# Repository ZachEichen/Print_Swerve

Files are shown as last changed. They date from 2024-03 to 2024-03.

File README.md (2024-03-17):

# Print Swerve: A fully customizable, Fully 3D printable Swerve drive for FTC 

This is a fully 3d printable swerve drive developed and used by FTC team [Robocracy](http://www.ftcrobocracy.org) in the 2018 FTC searon. It was primarily developed by [Nicolas Eichenberger](https://sites.google.com/view/neichenberger/) and [Zachary Eichenberger](https://github.com/ZachEichen).

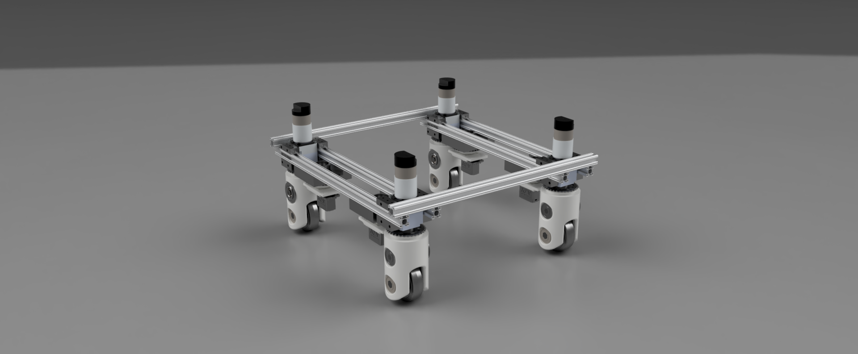
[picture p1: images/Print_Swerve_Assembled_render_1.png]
A render of the printable swerve assembled


As an FTC team we always strive to push the competition to the next level. We spent over a year developing our very own swerve drive to be a viable FTC drive base. 
After so much time and effort spent in development, we have developed the very first fully 3D printable swerve drive viable for FTC. Finally we have gotten this competition tested design to a stage of completion. 
Therefore, we are releasing this design for the benefit of the FTC community, and anyone else interested in an interesting omnidirectional robot drivetrain. 

## Using this repository: 

Both STL files for printing, and full CAD assemblies are avaliable for convenience. I have exported these in a variety of common CAD file formats in `CAD_source` (although they were made in fusion 360 so they might be a little wonky). 

Two STL files of the main module are avaliable. Our assembly guide assumes the use of 1/2" flanged thunderhex bearings from Vexpro. To use this part, print `STL_files/ModuleBody.stl`. Otherwise, you can use radial thunderHex bearings, and substitute `Tube_Body_Radial_Bearings.stl`.

You can also have a look at the associated thingiverse part, [found here](https://www.thingiverse.com/thing:2998874/files), and Nicky's [blog post](https://sites.google.com/view/neichenberger/projects/robotics-projects/swerve-drive-saga)  on the build process. 

## Glamour shots 

https://github.com/ZachEichen/Print_Swerve/assets/14967701/36f6d081-fa3b-49ac-bc39-774735051941

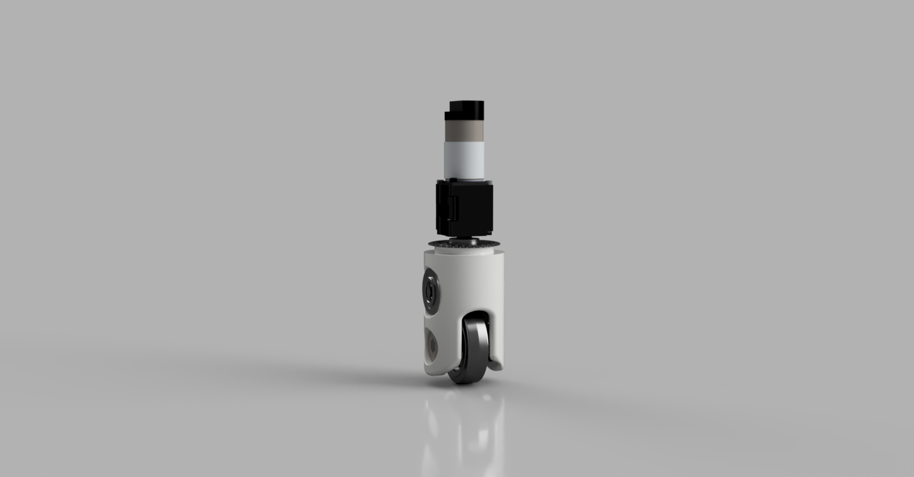
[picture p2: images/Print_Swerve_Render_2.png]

Glam shot

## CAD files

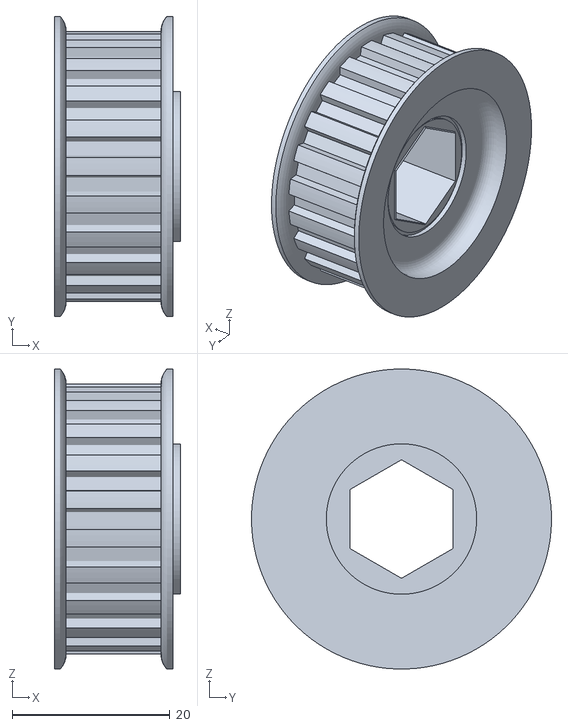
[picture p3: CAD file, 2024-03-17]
STL_files/ModuleBottomPulley.stl
16.0 x 38.0 x 38.0

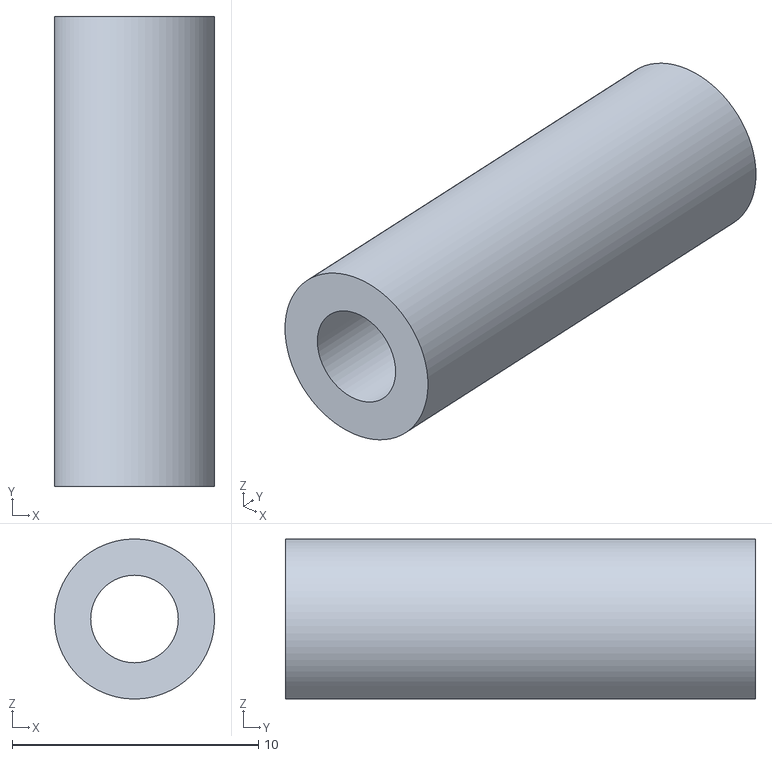
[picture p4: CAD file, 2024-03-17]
STL_files/Steering_Module_Standoffs.stl
6.50 x 19.1 x 6.49

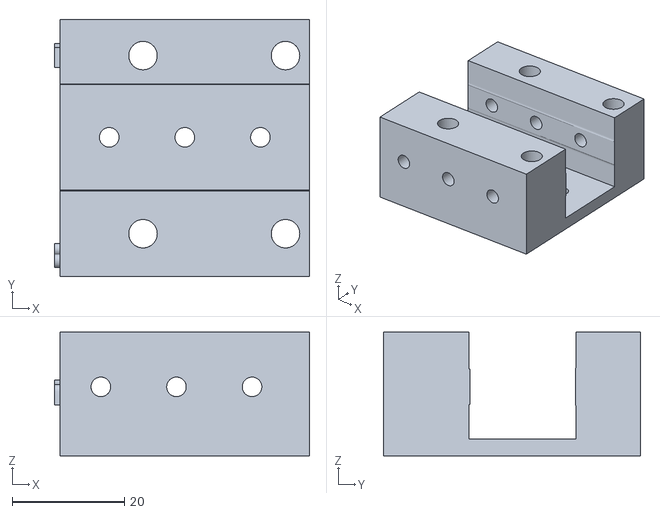
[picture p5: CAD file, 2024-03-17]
STL_files/RightMotorMount.stl
45.5 x 45.7 x 22.1

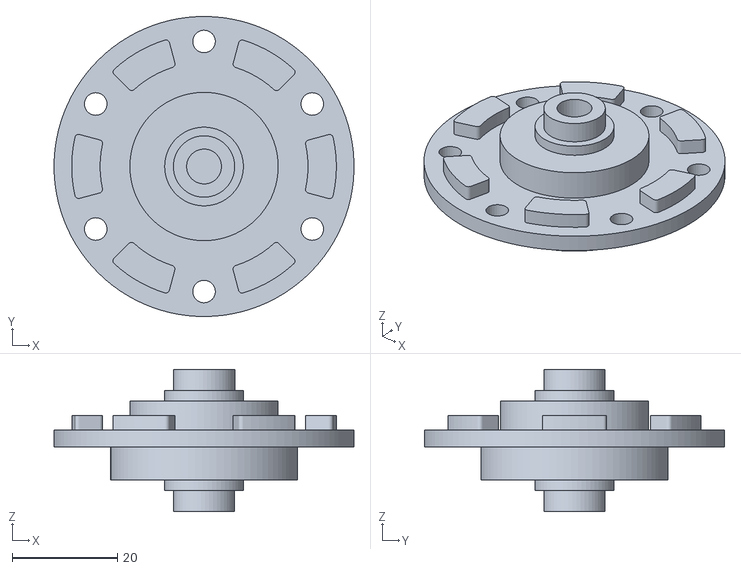
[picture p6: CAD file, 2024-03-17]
STL_files/Sprocket_Adapter_Plate.stl
57.1 x 57.1 x 27.1

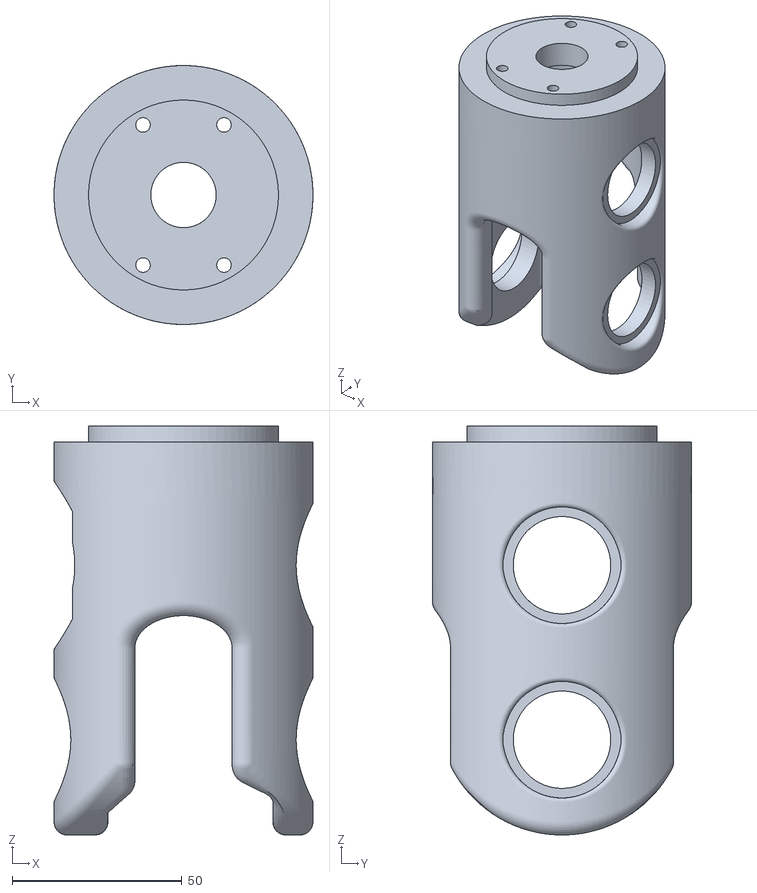
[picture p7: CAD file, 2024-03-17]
STL_files/ModuleBody.stl
76.2 x 76.2 x 120.3

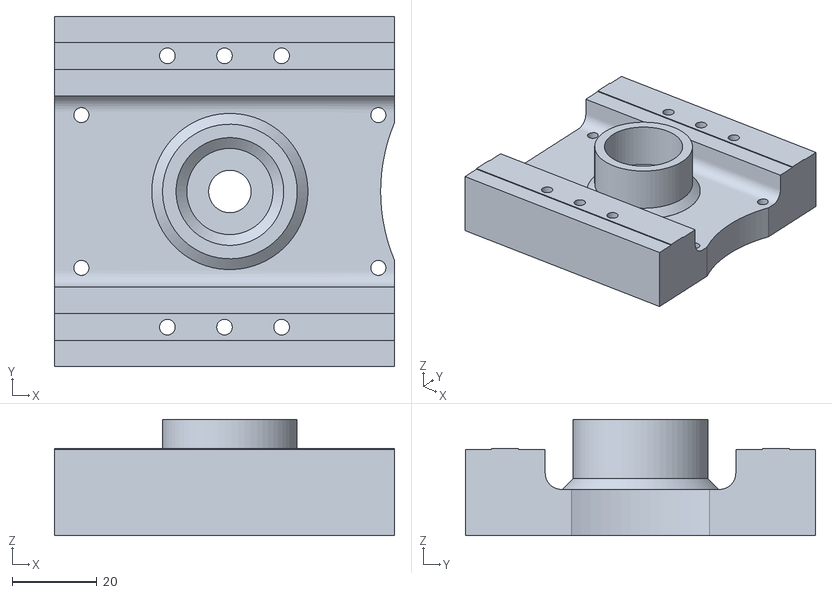
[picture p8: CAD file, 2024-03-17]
STL_files/Steering_Module_Top_Plate.stl
80.2 x 82.6 x 27.4

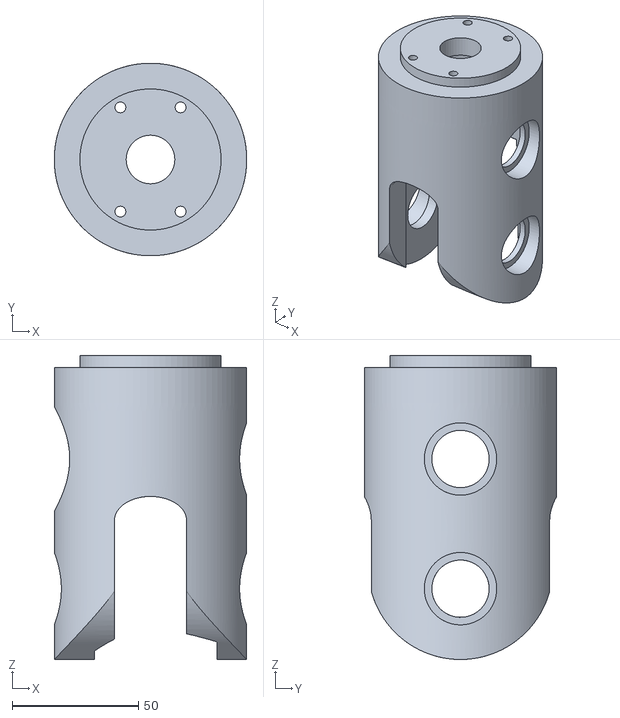
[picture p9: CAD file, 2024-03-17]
STL_files/Tube_Body_Radial_Bearings.stl
76.2 x 76.2 x 120.3

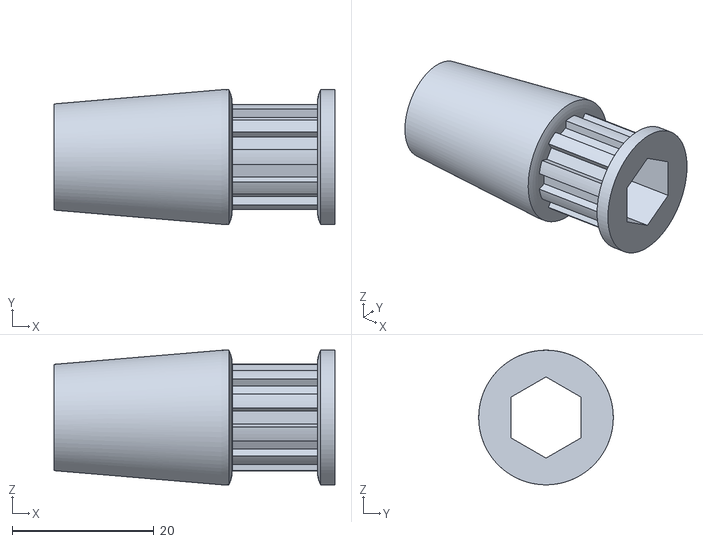
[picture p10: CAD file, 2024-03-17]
STL_files/ModuleTopPulley.stl
39.7 x 19.0 x 19.0

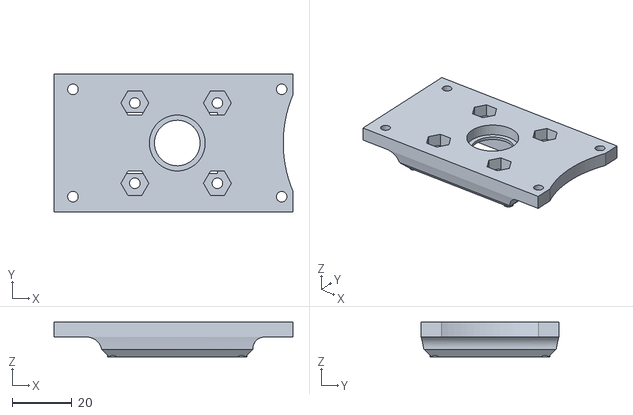
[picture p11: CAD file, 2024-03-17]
STL_files/Steering_Module_Bottom_Plate.stl
80.2 x 46.2 x 11.6

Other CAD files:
STL_files/leftMotorMount.stl

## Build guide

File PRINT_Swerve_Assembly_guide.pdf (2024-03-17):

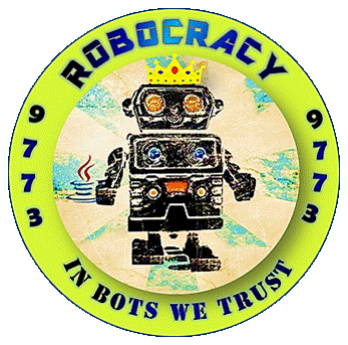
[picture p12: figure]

# PRINT Swerve Drive for FTC

Designed and built by Team FTC 9773, Robocracy 4H Westchester, NY
ftcrobocracy@gmail.com
March 2018

# 1.Introduction

We provide here the full instruction on how to build your very own PRINT Swerve. This innovative swerve drive is entirely build out of 3D printed part, no CNC machining required. It uses FRC-level gears and sprockets (VEX-pro) for unprecedented reliability. We use a novel “Tower” design where the drive motor is directly mounted on top of the drive to deliver the compact footprint needed for FTC robots. To our knowledge, this is the first 3D printable, nearly-indestructible integrated swerve drive, optimized for the tight spaces using FRC-level gears. We named it PRINT Swerve module, for PRintable INtegrated Tower Swerve.

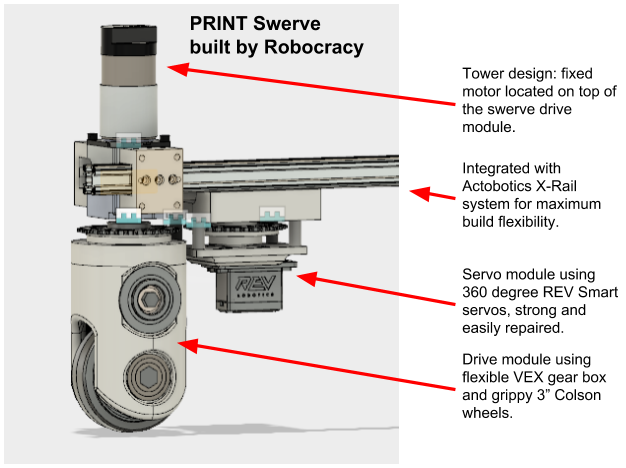
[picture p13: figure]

You will need between 2 to 4 Swerve Drive Modules, typically 4. A Swerve Drive Module consists of two assemblies: a Motor Module and a Steering Module. The two are connected by a chain and are mounted on a chassis made of Actobotics X-Rails. The Colson wheel has a 3” diameter, sufficient for climbing most obstacles. Once you have assembled the 122 parts, you will own your very own PRINT Swerve drive.

Section 2 list the parts that you need to build one Swerve Drive. For each part, we list a vendor and its part number. Section 3 lists the parts that you will need to 3D print, and Section 4 details the tools required to build it. Section 5 provides a step by step description and illustration of how to build the Swerve Motor Module. Section 6 details how to build the Swerve Steering Module. Section 7 let you assemble the two modules on the X-rails.

# 2. List of parts

## 2.1 Parts for the Swerve Motor Module

Part name | # | Part description | Part number
Motor (1) | 1 | AndyMark NeveRest Classic Motor | AndyMark part am-3104
Gear box (2) | 1 | VersaPlanetary Gearbox with ⅜ hex shaft with recommended 9:1 gear ratio. You may want to buy a spare VersaPlanetary 3/8" Hex Output Shaft as you will need to tap the end. | VEX PRO ● Base kit ⅜ Hex output, part 217-4974 ● 9:1 Gear kit part 217-3106 ● Ring gear part 217-2816 ● Additional shaft part 217-2894 (optional)

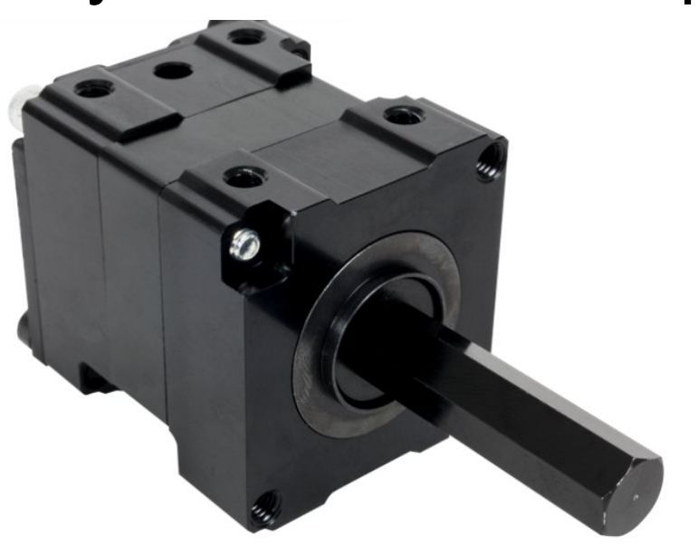
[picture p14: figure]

⅜” Flanged ball bearing (3) | 2 | Flanged ball bearing for ⅜ shaft, 0.375" Hex ID x 1.125" OD x 0.313" WD | VEX-pro part 217-2735

PRINT Swerve Drive for FTC, by Team FTC 9773, Robocracy 4H.
Web: ftcrobocray.org, email: ftcrobocracy@gmail.com. | Page 2 of 20.

Thunderhex flanged ball bearing (4) | 2 | Flanged ball bearing for 1/2" ThunderHex ½” ID x 1.125" OD x 0.313" WD | VEX-pro part 217-4006
Alternator ball bearing (5) | 1 | AB Open Alternator Ball Bearing 18.7mm x 37mm x9mm | VXB part 6904DW
Large flanged ball bearing (6) | 1 | Flanged ball bearing for 3/4" Shaft Diameter, 1-5/8" OD | McMaster part 6384K367
Bevel gear (7) | 2 | 15t Steel Bevel Gear, 12DP, 3/8" Hex Bore | VEX-pro part 217-3344
Wheel (8) | 1 | Colson Performa wheel, 3" x 0.875", 1/2" Hex Bore | VEX-pro part 217-4047
Web: ftcrobocray.org, email: ftcrobocracy@gmail.com. | Page 3 of 20.

Timing belt (9) | 1 | 185mm timing belt Dust-Free Timing Belt, T5 Series, Trade No. T5-185-1 | McMaster part 1679K441
½” Thunderhex shaft (10) | 2.6” | thunderhex shaft ½” | VEX-pro part 217-4002
⅜” Hex shaft (11) | 2.75” | Hex shaft ⅜” | VEX-pro part 217-3310
Sprocket (12) | 1 | 32t Aluminum Plate Sprocket for #25 Chain, 1-1/8" Bearing Bore | VEX-pro part 217-2690
Chain (13) | 12” | #25 Standard Roller Chain (10 feet) | VEX-pro part 217-2775
Web: ftcrobocray.org, email: ftcrobocracy@gmail.com. | Page 4 of 20.

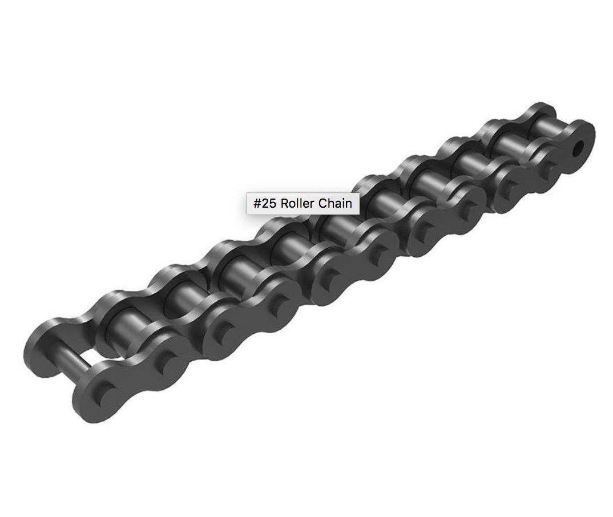
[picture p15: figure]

¼” Screw (14) | 2 | 18-8 Stainless Steel Button Head Hex Drive Screw, 1/4"-20 Thread Size, 3/4" Long | McMaster part 92949A540
#8 Screw (15) | 3 | 18-8 Stainless Steel Button Head Hex Drive Screw, 8-32 Thread Size, 1/2" Long | McMaster part 92949A194

Long #6 Screw and nylon nut (part 16) | 4 | 18-8 Stainless Steel Button Head Hex Drive Screw, 6-32 Thread Size, 1" Long 316 Stainless Steel Nylon-Insert Locknut, Super-Corrosion-Resistant, 6-32 Thread Size | McMaster parts 92949A153 and 90715A007
Large #8 washer (17) | 1 | 316 Stainless Steel Washer, Oversized, Number 8 Screw Size, 0.188" ID, 1" OD | McMaster part 91525A268
Small #8 | 1 | 316 Stainless Steel Washer, Oversized, | McMaster part
Web: ftcrobocray.org, email: ftcrobocracy@gmail.com. | Page 5 of 20.

washer (18) | | Number 8 Screw Size, 0.172" ID, 0.5" OD | 91525A318

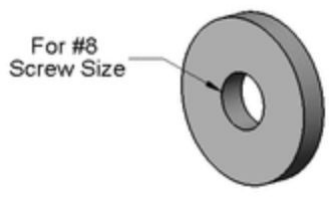
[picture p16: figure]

Very small #8 washer (19) | 1 | 18-8 Stainless Steel Washer for Number 8 Screw Size, 0.172" ID, 0.375" OD | McMaster part 92141A009
¼” washer (20) | 2 | 316 Stainless Steel Washer for 1/4" Screw Size, 0.281" ID, 0.625" OD | McMaster part 90107A029

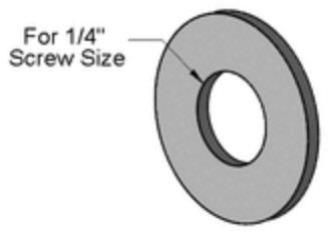
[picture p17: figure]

Hex spacer (21) | 1 | 1/2" Acetal Spacer - 1/2" Hex (10-pack) | VEX-pro part 217-3261
Hex spacer (22) | 1 | 1/8” Acetal Spacer - 3/8" Hex (10-pack) (can use a 1/2” Hex if you have them already) | VEX-pro part 217-3256
Loctite (23) | 1 | Tube/bottle of blue loctite | Hardware store
Web: ftcrobocray.org, email: ftcrobocracy@gmail.com. | Page 6 of 20.

## 2.2. Parts for the Swerve Steering Module

Part name | # | Part description | Part number
Servo (100) | 1 | Smart REV servo | REV part REV-41-1097
Servo plate (101) | 1 | Standard Servo Plate A | Servocity part 575112
Absolute encoder (102) | 1 | Absolute encoder with cable | AndyMark part am-2899
3/4“ 6-32 Screw (103) | 4 | Black-Oxide Alloy Steel Socket Head Screw, 6-32 Thread Size, 3/4" Long | McMaster part 91251A151
Locknut (104) | 11 | 316 Stainless Steel Nylon-Insert Locknut, Super-Corrosion-Resistant, 6-32 Thread Size | McMaster part 90715A007
Ball bearings (105) | 2 | 12x18x4 Metal Shielded Bearing 6701-ZZ | Various vendors, e.g. Neweggs.com
Web: ftcrobocray.org, email: ftcrobocracy@gmail.com. | Page 7 of 20.

Servo gear (106) | 1 | 48P, 25T 3F Spline Servo Mount Gears (Metal) | Servocity part RSA48-FMG-15

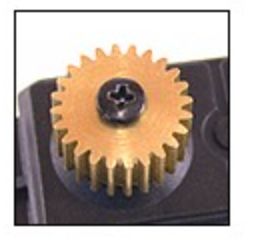
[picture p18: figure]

3/8" 6-32 screws (107) | 4 | Black-Oxide Alloy Steel Socket Head Screw, 6-32 Thread Size, 3/8" Long | McMaster part 90128A855
Sprocket (108) | 1 | 32t Aluminum Plate Sprocket for #25 Chain, 1-1/8" Bearing Bore | VEX-pro part 217-2690
3/8" 6-32 screw with button head (part 109) | 3 | Button Head Hex Drive Screw, Black-Oxide Alloy Steel, 6-32 Thread, 3/8" Long | McMaster part 91255A146
1 ½" 6-32 screws (110) | 4 | Black-Oxide Alloy Steel Socket Head Screw, 6-32 Thread Size, 1-1/2" Long | McMaster part 91251A157
Web: ftcrobocray.org, email: ftcrobocracy@gmail.com. | Page 8 of 20.

## 2.3. Parts for the Swerve Chassis

Part name | # | Part description | Part number
Xrail (part 150) | 2 | Actobotics® X-Rail of desired length (here 18”). Need 2 rails per pair of swerve drives | Servocity part 565062

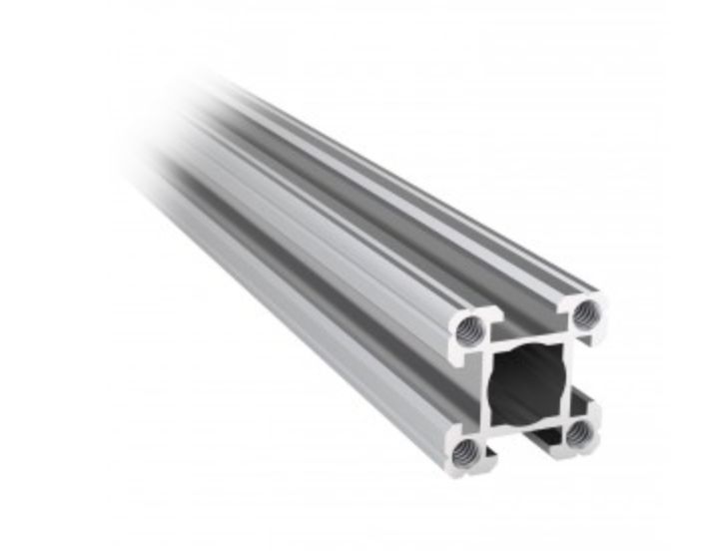
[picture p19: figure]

Xrail screw plates (part 151) | 6 | X-Rail Screw Plate (2 pack) | Servocity part 585757
3/8" 6-32 screws (152) | 12 | Black-Oxide Alloy Steel Socket Head Screw, 6-32 Thread Size, 3/8" Long | McMaster part 90128A855
3/4" 6-32 screws (153) | 6 | Black-Oxide Alloy Steel Socket Head Screw, 6-32 Thread Size, 3/4" Long | McMaster part 92949A151
1 ¼” 10-32 screw (154) | 8 | 18-8 Stainless Steel Button Head Hex Drive Screw, 10-32 Thread Size, 1-1/4" Long | McMaster part 92949A272
Web: ftcrobocray.org, email: ftcrobocracy@gmail.com. | Page 9 of 20.

# 3. Printed Parts

## 3.1 Printed Parts for Swerve Motor Module

Part Name | Description

Swerve motor module body (201)

Top pulley (202)

Bottom pulley (203)

X rail adapter (2x) (204)

Web: ftcrobocray.org, email: ftcrobocracy@gmail.com. | Page 10 of 20.

## 3.2 Printed Parts for Steering Module

Part Name | Description

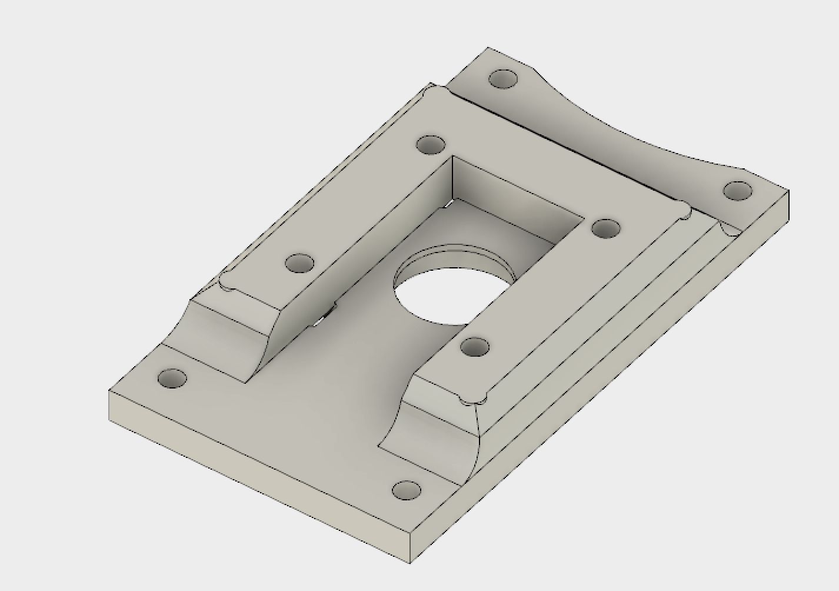
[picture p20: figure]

Steering module bottom plate (301)

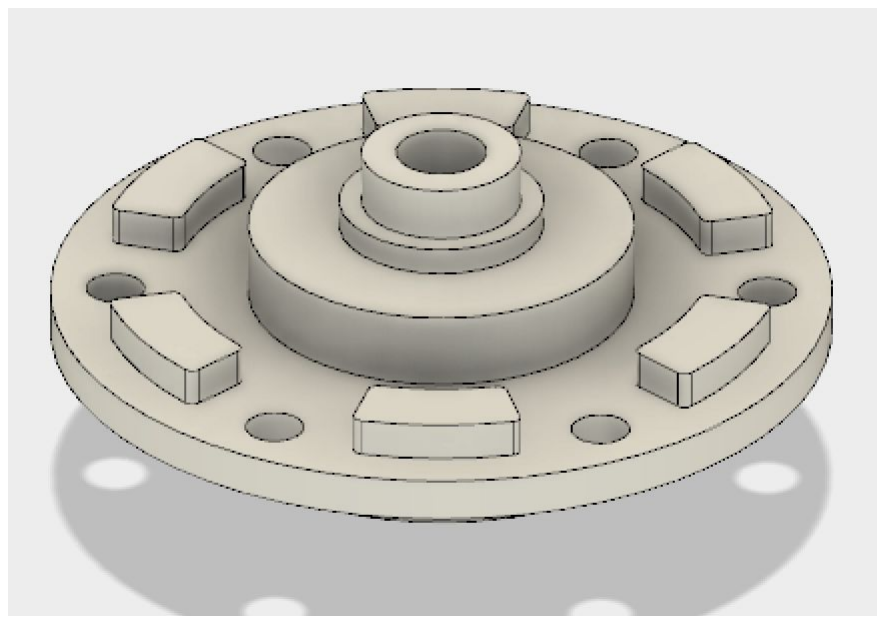
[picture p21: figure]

Sprocket adapter plate (302)

Steering module Top plate (303)

Web: ftcrobocray.org, email: ftcrobocracy@gmail.com. | Page 11 of 20.

3d printed standoffs (4x)
(304)

# 4. Tools

1. 3D printer
2. Tap tool for 8-32 and ¼”-20 threads
3. Dremel with sandpaper bit and/or files of various sizes
4. Hex screwdriver and wrenches

# 5. Assembling a Swerve Motor Module

Step 1: Prepare Shafts
1. Cut ½” shaft (part 10) to 2.6” length.
2. Cut ⅜” shaft (part 11) to 2.75” length.
3. Tap ½” shaft ends with ¼-20 thread and verify that screw (part 14) fits.
4. Drill and tap ⅜” shaft ends with 8-32 thread and verify that screw (part 15) fits.
Step 2: Prepare Motor
1. Remove VersaPlanetary 3/8" Hex Output Shaft from gearbox (part 2).
2. Drill and tap ⅜” shaft end with 8-32 thread and verify that screw (part 15) fits.
3. Build gearbox and attach to motor (part 1) using VEX-pro instructions.
Web: ftcrobocray.org, email: ftcrobocracy@gmail.com. | Page 12 of 20.

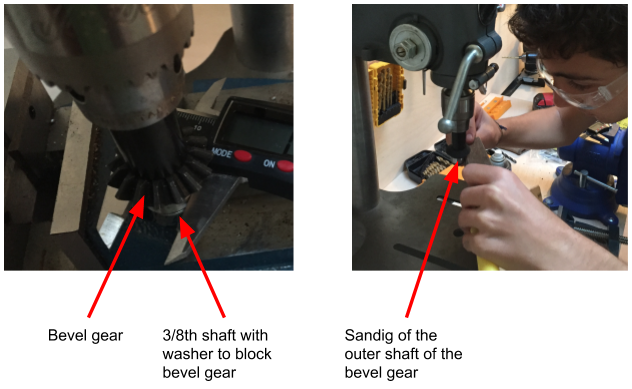
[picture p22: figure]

Step 3: Prepare one bevel gear
1. The outer shaft of one of the two bevel gears (part 7) must be sanded down to fit inside alternator ball bearing (part 5). Best is to use a short piece of ⅜” shaft with a washer at one end. Place the bevel gear on the shaft on the end of the washer, insert the shaft on the other end in a drill press, and carefully sand the outer shaft of the bevel gear until the ball bearing fits snuggly. If too snug, the ball bearing will not rotate easily. If too loose, the swerve module with wobble. This is a critical step.
Step 4: Print swerve motor module parts
1. Print swerve motor module (part 201), with a high infill (>30%) and a shell line number (>5) and with support for the ball bearing holes. We strongly recommend Polymaker’s PC-Max filament, as it is essentially Lexan. Note that not all printer support PC filaments. You should also print several smaller parts as you don’t want to experiment with the large swerve module.
Web: ftcrobocray.org, email: ftcrobocracy@gmail.com. | Page 13 of 20.

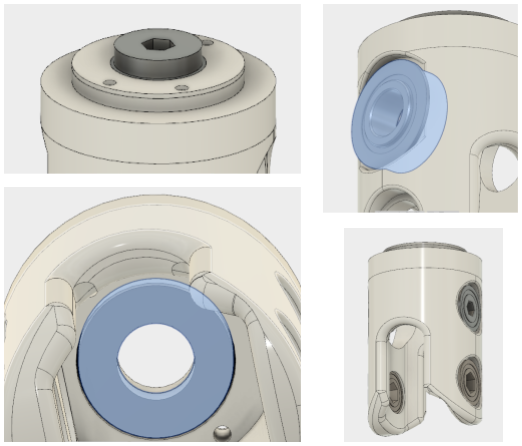
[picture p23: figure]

2. Fit all the ball bearings in the bearing holes in the module. Key is to get the vertical bearings (parts 3 & 5) to fit snuggly. If too snug, the shaft will not turn smoothly; if too loose, the module will wobble. Best is to use a dremel with a sandpaper bit, or a drill bit of the right size. The CAD model tuned the holes to be a bit snug, as the filaments do not always cool off to a round hole (we often witnessed an oval shape). So sanding is key to get the bearing to fit snuggly.
3. Print the other 2 pulleys (parts 202 & 203).
Web: ftcrobocray.org, email: ftcrobocracy@gmail.com. | Page 14 of 20.

Step 5. Assemble swerve motor module

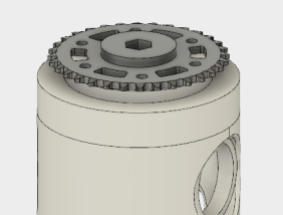
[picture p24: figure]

1. Assemble the sprocket. Insert top shaft ball bearing (part 3) with flange down, lock with one sprocket (part 12) and screw (part 16) with screw head on side of sprocket and nut inside the swerve module.

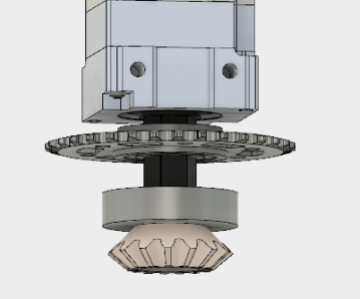
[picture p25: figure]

2. Attach the motor. Insert the 1/8“ spacer (part 22), inner shaft ball bearing (part 5), then slide the sanded down bevel gear (part 7, machined in Step 3) inside the inner shaft ball bearing. Then slide the motor and gear assembly (parts 1 & 2, machined in step 2). Then insert screw (part 15) with washer (part 19) to lock the assembly. Use locktite on the screw as you definitely don’t want that screw to loosen. Picture above shows the assembly without the 3D printed part.
Web: ftcrobocray.org, email: ftcrobocracy@gmail.com. | Page 15 of 20.

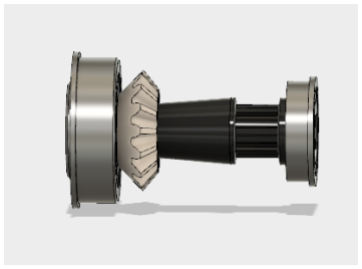
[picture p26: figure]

3. Attach the top horizontal shaft. Insert the second bevel gear (part 7) inside the large flanged ball bearing (part 6), with the bevel gear on the side without the flange. Insert the bearing inside the swerve module, and then partly slide the ⅜” shaft (part 11, machine in
Step 1). Then insert the top pulley (part 202) on the shaft and slide the timing belt (part 9). Complete by inserting the shaft ball bearing (part 3) and continue pushing the shaft. Then use the #8 screw and washer (parts 15 & 17) on the side of the large ball bearing, and use the #8 screw and washer (parts 15 & 18) on the side of the small ball bearing. Use loctite on the screws. Picture above shows the assembly without the 3D printed part.

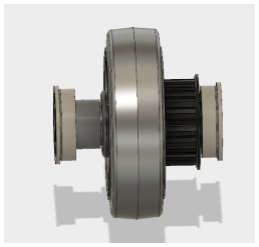
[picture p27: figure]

4. Attach the bottom horizontal shaft. Insert the shaft flanged ball bearing (part 4) on the side of the belt. Slide the shaft (Part 10, machined in Step 1) inside the ball bearing, and slide the bottom pulley (part 203). The pulley is asymmetrical; the side with the small integrated washer goes flush against the bearing; the side with the concave hole will go against the wheel. Insert the belt on the pulley. Slide the wheel (Part 8) on the shaft, and
Web: ftcrobocray.org, email: ftcrobocracy@gmail.com. | Page 16 of 20.

add the hex washer (Part 21). Insert the second ball bearing (Part 4) on the swerve motor module. Then use the ¼” screws and washers (parts 14 & 20) with loctite. Picture above shows the assembly without the 3D printed part.

# 6. Assembling a Swerve Steering Module

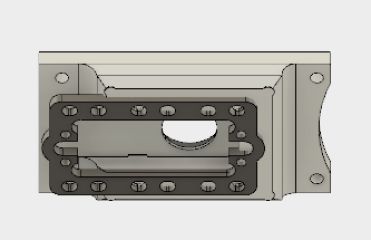
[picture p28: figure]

1. Attach the servo plate (part 101) on printed steering module bottom plate (part 301) on the bottom side, with #6 3/4“ (part 103) and nut (part 104). Nut will be flush inside the 3D printed part. Above picture shows the result. You may have to insert washers, or shorten the screws.

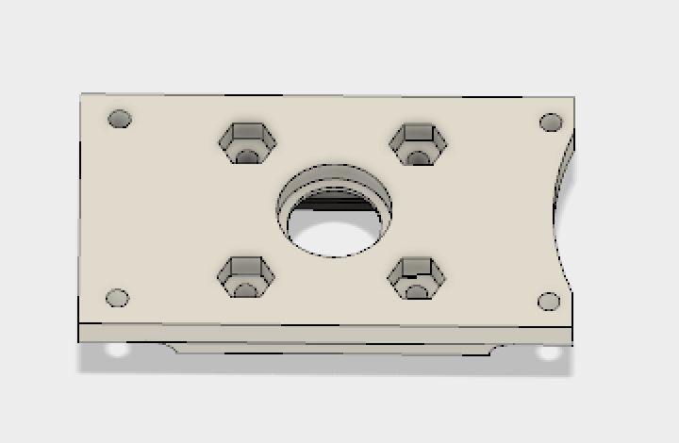
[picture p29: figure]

2. Insert the ball bearing (part 105) on the top side of steering module (part 101), depicted above.
Web: ftcrobocray.org, email: ftcrobocracy@gmail.com. | Page 17 of 20.

3.

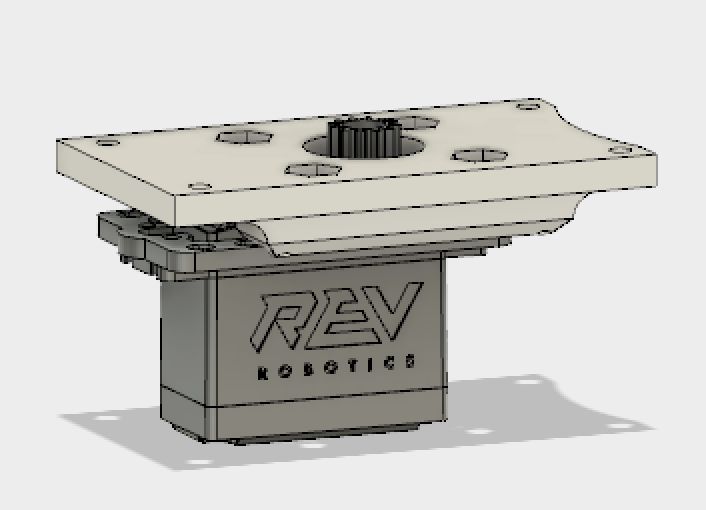
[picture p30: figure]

4. Attach the REV servo on the assembly by using 4 3/8" 6-32 (part 107). You should get the part as shown by the above drawing.

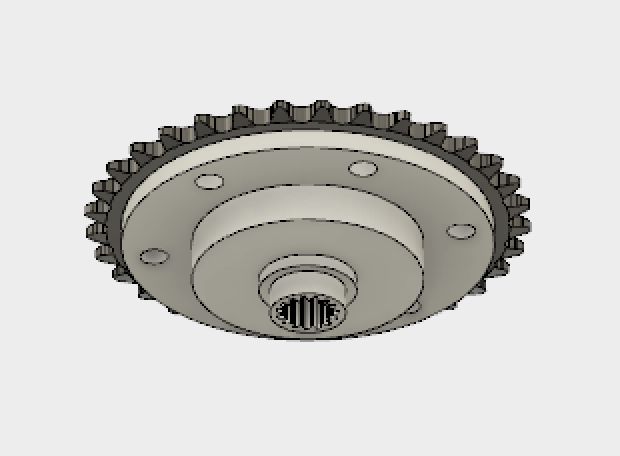
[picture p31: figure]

5. Insert the servo gear (part 106) inside the sprocket adapter plate (part 302), and attach sprocket (part 108) on the other side with 3 button head screws (part 109) and associated locknuts. Result should look like the above drawing (servo gear and screws not shown here).

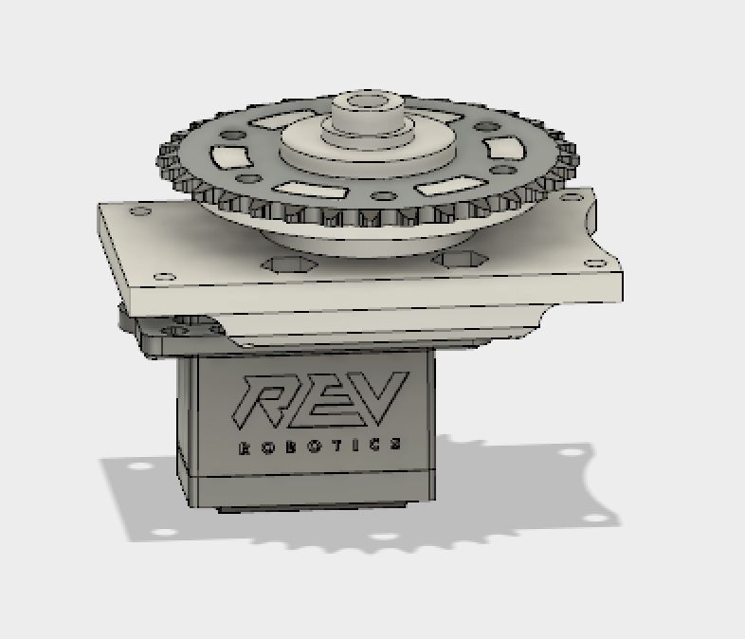
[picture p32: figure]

Web: ftcrobocray.org, email: ftcrobocracy@gmail.com. | Page 18 of 20.

6. Slide sprocket adaptor on on the steering module (part 101). Result shown above.

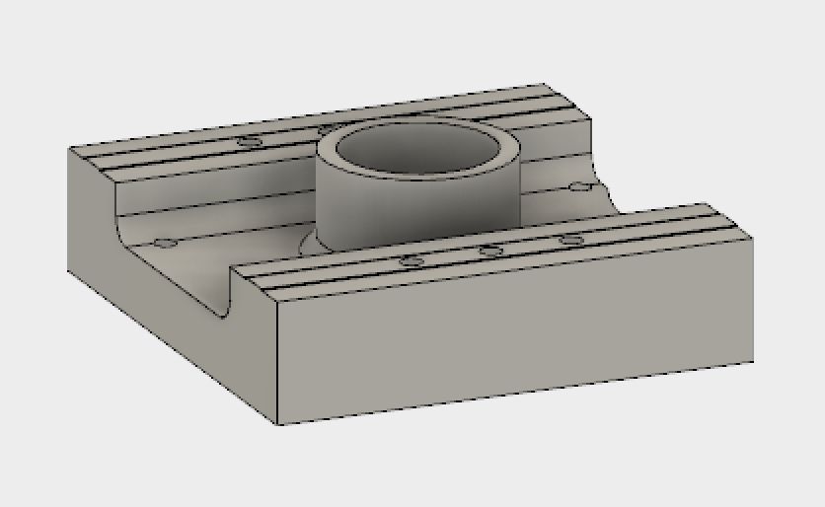
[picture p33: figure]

7. Now working with the Steering module Top plate (part 303). Insert the second ball bearing (part 105) into the lower middle hole. Then add the Absolute encoder (part 102). Attach firmly.
8. Complete the assembly by using 4 1½“ inch screws (part 110) through the above part, into the 4 tubes (part 304) and into the lower assembly, and attached with 4 locknuts. It is sometime better to also insert the chain now before tightening the assembly. The result should look as below.

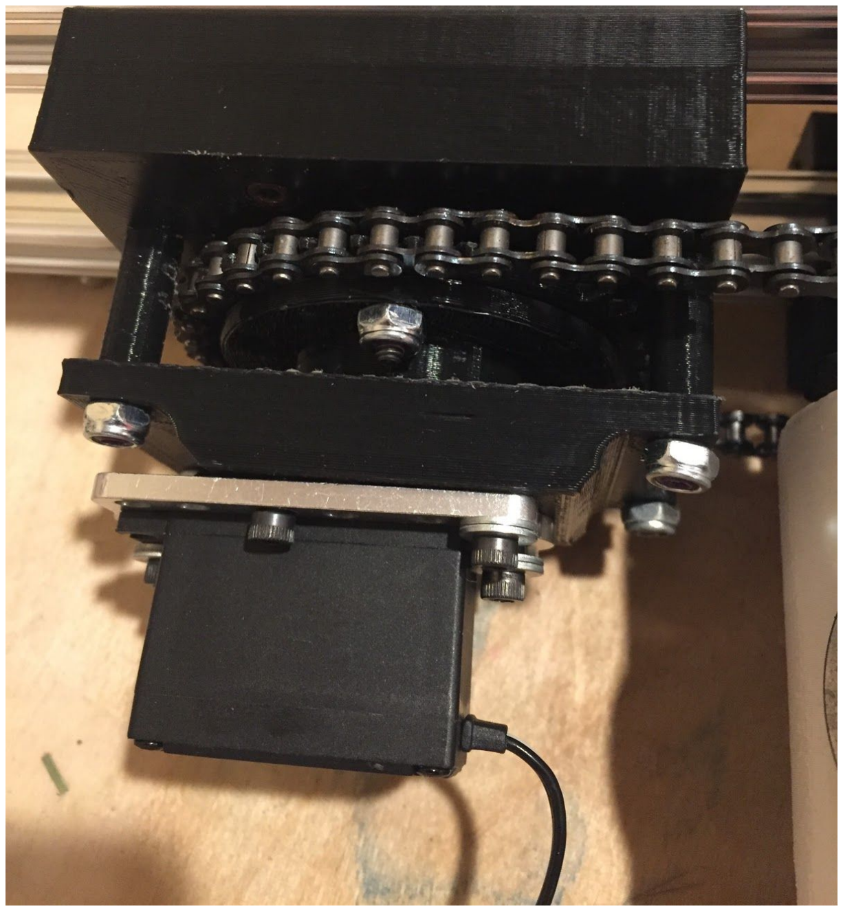
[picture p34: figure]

# 7. Assembling the Chassis with Swerve Modules

1. Attach the servo module on the xrails (part 150) using two screw plates (151) and 6 ¾” 6-32 screws (part 153) on both xrails.
2. Attach the 4 brackets (part 204) on both side of the VEX-pro gear box of the swerve module using the 8 10-32 screws (part 154). You may have to adjust the length of the screws so that they don’t damage the gearbox while being sufficiently tight.
3. Attach the serve module using 4 screw plates (151) and 12 6-32 screws (part 152).
Web: ftcrobocray.org, email: ftcrobocracy@gmail.com. | Page 19 of 20.

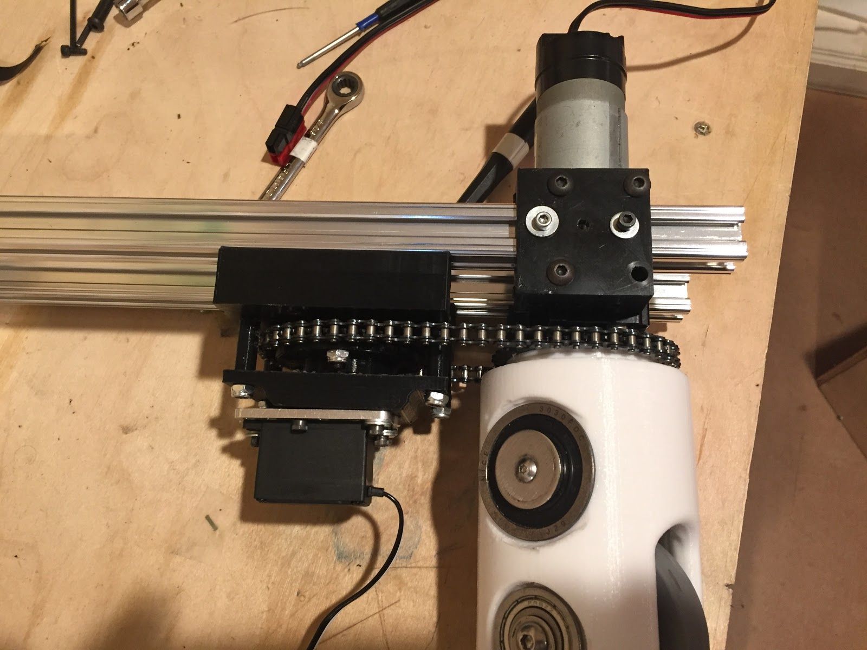
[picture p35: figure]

Voilà, you are now the proud owner of a PRINT swerve module. Hope you enjoyed the process. Feel free to contact us at any time for suggestions or help.

Web: ftcrobocray.org, email: ftcrobocracy@gmail.com. | Page 20 of 20.
